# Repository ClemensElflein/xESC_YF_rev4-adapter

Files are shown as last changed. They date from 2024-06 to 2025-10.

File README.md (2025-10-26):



<!-- PROJECT SHIELDS -->
<!--
- Markdown "reference style" links for readability.
- Reference links are enclosed in brackets [ ] instead of parentheses ( ).
  (See the bottom of this document for the declaration of the reference variables)
-->
[][contributors-url]
[][forks-url]
[][stars-url]
[][issues-url]
[][license-url]

<!-- PROJECT LOGO -->
<br />
<div align="center">
<h3 align="center">xESC YardForce (Rev4) adapter for <a href="https://github.com/ClemensElflein/OpenMower">OpenMower</a></h3>

  <p align="center">
    Simple xESC adapter for stock Rev4 (built 2017) blade-motor<br>
    (the one with a internal motor controller under his cap)
    <br />
  </p>

  |             v1.x Hardware              |             v2.x Hardware              |
  | :------------------------------------: | :------------------------------------: |
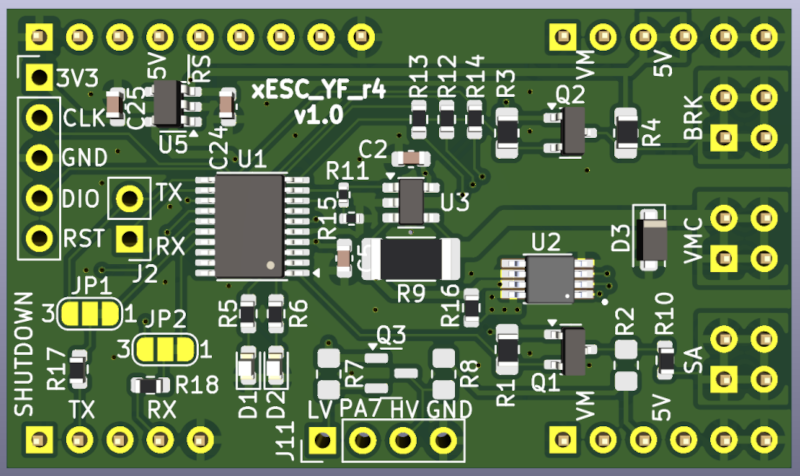
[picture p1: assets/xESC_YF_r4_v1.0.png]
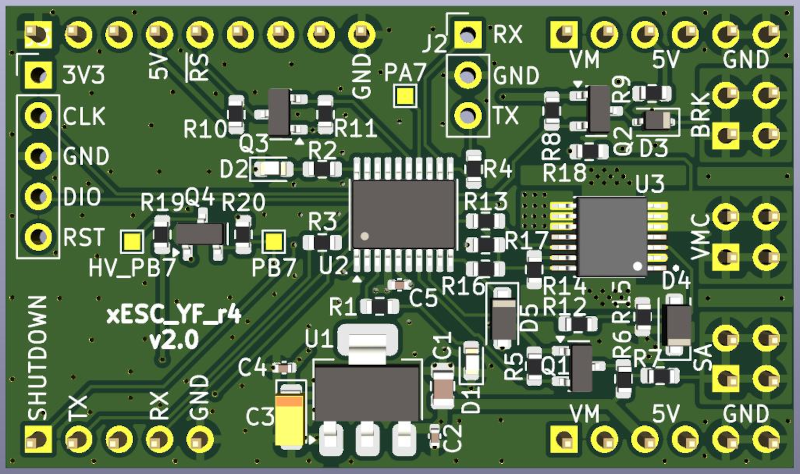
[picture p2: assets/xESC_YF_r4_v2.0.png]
  |  |  |

</div>

<!-- ABOUT THE PROJECT -->
## About The Project

<a href="assets/rev4-mow-motor.jpg">
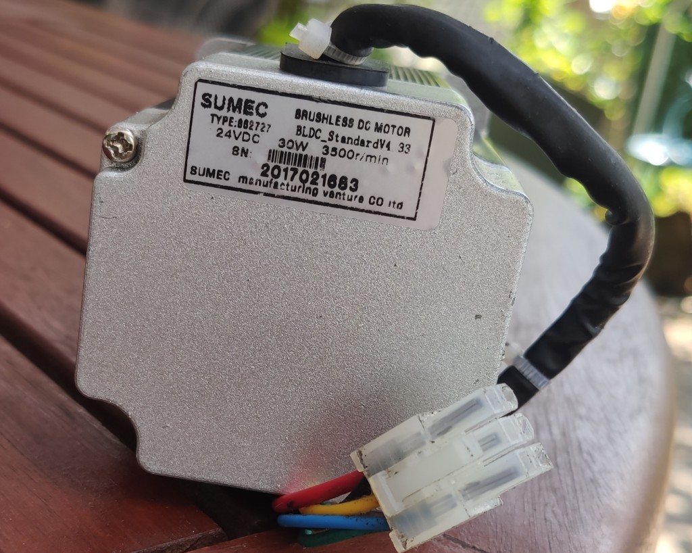
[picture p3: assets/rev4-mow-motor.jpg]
Rev.4 Mow Motor
  </a>

Those who want use <a href="https://github.com/ClemensElflein/OpenMower">OpenMower</a> with an older YardForce "Rev. 4" (built 2017) model, fail with the stock Blade-Motor as it has an embedded motor-controller under it's cap.

It's not very difficult to use this motor:
- Remove stock driver controller
- Wire the coil cables directly
- Add a 5 pin cable to the motor hall sensors
- Connect them to OM's mow-motor-hall-input plug
and use OM's xESC.

But it's somehow "crafted" and you need to be capable to do these things.

As an alternative, this "Adapter" is thought to replace OM's default Mow- xESC.<br>
In addition to this adapter, it's nevertheless **required to exchange two cables of the mow motor cabling**. But this should be also possible for the untalented (see [Requirements](#requirements)).

<p align="right">(<a href="#readme-top">back to top</a>)</p>

## Requirements

<a href="assets/cross-gn-bk.jpg">
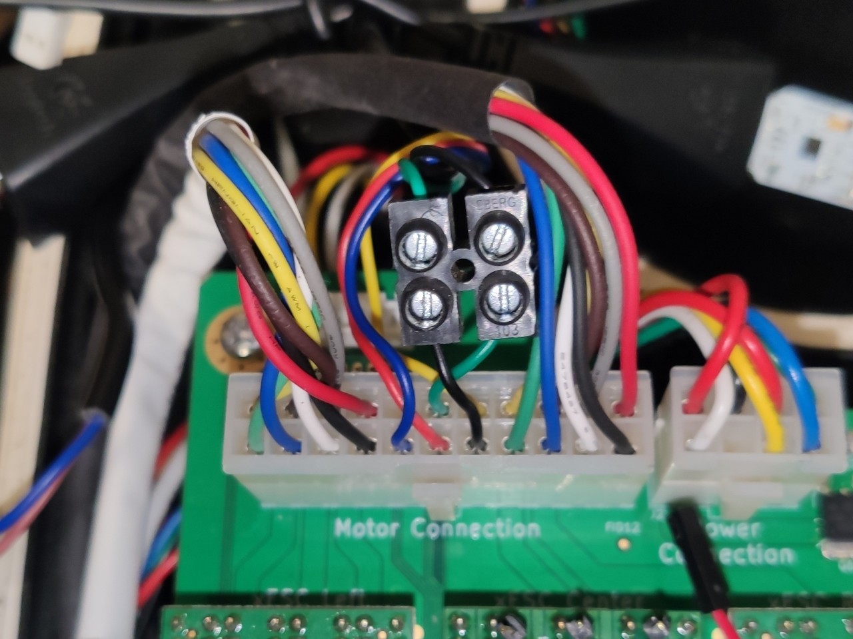
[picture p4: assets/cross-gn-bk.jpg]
Mandatory cable x-change
  </a>

**It's mandatory to cross the green and black mow-motor-cables!**

> [!WARNING]  
> **Never** plug or un-plug the mow-motor while the adapter is powered!

> [!WARNING]  
> Do **not** simply trust the cable colors!<br>
> Check the image and validate if your
> cables do have the same colors! If not adapt accordingly

Either exchange the pins within the plug, or do it the lazy way like me, with a luster terminal.
The latter has the advantage that you immediately see that you already crossed green/black.

## Prerequisites

* The compiled firmware, which can be found within the [Actions](https://github.com/ClemensElflein/xESC_YF_rev4-adapter/actions) section. Click the one you're intersted in (newest or tagged), scroll down to 'Artifacts', download and unzip to somewhere.
* As of writing, your openmower image has to be on edge version >= commit [0bfd489](https://github.com/ClemensElflein/open_mower_ros/commit/0bfd489401b3e659d183e6c1f9b557cb0d59d3c1) which happened on 2024-07-04

## Firmware Installation

### Requirements

* You need an ST-Link debugger/programmer, like one of the cheap "ST-Link V2" probes from one of the big online retailer.
* [STLINK Tools](https://github.com/stlink-org/stlink) >= v1.8.0 (earlier versions do **not** support the used STM32C0x MCU)

### Hardware Version Branding

Starting with hardware version 2.0, the adapters MCU needs to be branded by flashing a hardware config into the OTP area.

#### Branding Process:

1. **Generate** Hardware Config Binaries

   ```bash
   cd firmware/host-hw-config
   lbuild build
   scons
   ```

   This creates i.e.:
   - `hw_config_v1.0.bin` - Hardware v1.0 configuration
   - `hw_config_v2.0.bin` - Hardware v2.0 configuration
  
1. **Connect your ST-Link** to the adapter PCB. Do **not** connect the 3.3V pin if your adapter is already assembled to the OpenMower Mainboard and get powered by it!

1. **Flash** Hardware Config

   ```bash
   # Flash/Brand v2.0 config with ST-Link/V2
   STM32_Programmer_CLI -c port=SWD -d hw_config_v2.0.bin 0x1FFF7000
   ```

The branding process writes a small hardware information structure to the first two OTP dwords. **Take attention** that OTP flash can be written only once!

**Important Notes:**
- Branding only needs as well as "can" be done only **once per device**
- The branding **truly survives firmware updates** (because OTP flash can be written only once)
- Hardware Version 1.x boards don't need branding. Non-branded devices get assumed to be v1.0 hardware
<br>
<br>

**Firmware Installation Variants**

We've two options to install the firmware. Either via:<br>
- ST-Link debugger/programmer, for which you need to have access to the adapter PCB's SWDIO pins, or via
- Open-Mower's UART via STM32 internal bootloader (which can be done with a closed mower)

### Firmware Installation via ST-Link debugger/programmer

#### Flash

1. Connect your ST-Link probe to the adapter PCB. Do **not** connect the 3.3V pin if your adapter is already assembled to the OpenMower Mainboard and get powered by it!

2. Flash the adapter:
   ```sh
   st-flash --reset write firmware_xesc_yf_rev4.bin 0x08000000
   ```
   When done, st-flash should report 'Flash written and verified! jolly good!' (or similar) and immediately reboot.<br>

   **Only relevant for v1.x hardware:**

   > [!WARNING]  
   > Do not unplug now!
   
   On absolutely first firmware boot, it need to flash some settings to the MCU. You'll see some blink codes.<br>
   Do NOT unplug till you see:
   - 3 simultaneous blinks of the green+red LED (=success), following of a
   - quick blink of the red LED (=no motor connected) as well as a
   - normal green blink (=ROS not connected).
   
   The whole procedure will only take about 10 seconds. Once the procedure got processed it don't get triggered again for this MCU on future firmware flashes.

   If the board doesn't come up with blink signs, unplug and replug it. But once you see blink signs, do **not** unplug it before getting the described LED codes of the previous paragraph.   

<p align="right">(<a href="#readme-top">back to top</a>)</p>

### Firmware Installation via serial connection (UART)

Firmware flashing via UART is currently only possible with OpenMower V1 based hardware!

#### Requirements

* [STM32CubeProgrammer](https://www.st.com/en/development-tools/stm32cubeprog.html) is the tool we need to flash via UART. But because we like to use it with our OpenMower's Raspberry-Pi, we need it in `aarch64` architecture. Unfortunately (as well as unbelievable) ST's programmer tool for ARM CPU's isn't available *for* ARM CPU's/architectures!!<br>
So we need to trick a little bit, and for this you need a non-arm Linux machine (x86_64).<br>
  1. Download [STM32CubePrg-Lin](https://www.st.com/en/development-tools/stm32cubeprog.html) package with (or to) a x86_64 Linux machine
  2. Unpack and install it on the x86_64 Linux machine
  3. Pack (zip, tar, ...) the installed binaries from where you just installed them
  4. Copy that package to your Raspberry-Pi and unpack it to somewhere. I placed mine to /opt/STM32CubeProgrammer
* [box64](https://github.com/ptitSeb/box64) to be able to run the STM32CubeProgrammer's x86_64 binary with our aarch64 architecture.<br>
Luckily they do have pre-build [Debian packages](https://github.com/ptitSeb/box64/blob/main/docs/COMPILE.md#debian-based-linux). Please follow their instruction.

Once *box64* got installed, you should be able to start the STM32Programmer CLI i.e. via: `/opt/STM32CubeProgrammer/bin/STM32_Programmer_CLI`

### Flash

1. Login to your OpenMower Raspberry-Pi and stop openmower:<br>
   `sudo systemctl stop openmower`
   
2. Configure Raspberry-PI's serial device where the adapter is connected to, which is normally */dev/ttyAMA3*:<br>
   `stty -F /dev/ttyAMA3 115200 raw`
   
3. Now trigger the current running adapter firmware to do a reboot into the bootloader via:<br>
    `echo -e "\x00Reboot into Bootloader" > /dev/ttyAMA3`

4. Check if STM32 MCU is now in bootloader mode (Step 3. was successful):<br>
   `/opt/STM32CubeProgrammer/bin/STM32_Programmer_CLI -c port=/dev/ttyAMA3`<br>
   Should output something like:<br>

   ```
      -------------------------------------------------------------------
                        STM32CubeProgrammer v2.16.0                  
      -------------------------------------------------------------------

   Serial Port /dev/ttyAMA3 is successfully opened.
   Port configuration: parity = even, baudrate = 115200, data-bit = 8,
                       stop-bit = 1.0, flow-control = off
   Activating device: OK
   Board       : --
   Chip ID: 0x443 
   BootLoader protocol version: 3.1
   Device name : STM32C01x
   Flash size  : 32 KBytes (default)
   Device type : MCU
   Revision ID : --  
   Device CPU  : Cortex-M0+
   ```

5. Flash:<br>
   `/opt/STM32CubeProgrammer/bin/STM32_Programmer_CLI -c port=/dev/ttyAMA3 -w firmware_xesc_yf_rev4.bin 0x08000000`

6. Reset the device (start our newly flashed program):<br>
   `/opt/STM32CubeProgrammer/bin/STM32_Programmer_CLI -c port=/dev/ttyAMA3 --go 0x08000000`

   **Only relevant for v1.x hardware:**

   > [!WARNING]  
   > Do not power-off now!
   
   On absolutely first firmware boot, it need to flash some settings to the MCU. You'll see some blink codes.<br>
   Do NOT unplug till you see:
   - 3 simultaneous blinks of the green+red LED (=success), following of a
   - quick blink of the red LED (=no motor connected) as well as a
   - normal green blink (=ROS not connected).
   
   The whole procedure will only take about 10 seconds. Once the procedure got processed it don't get triggered again for this MCU on future firmware flashes.

7. Finally start openmower again:<br>
   `sudo systemctl start openmower`

<p align="right">(<a href="#readme-top">back to top</a>)</p>

## OpenMower Config

### OpenMower V1 based Hardware (mower_config)

Lastly, you need to add the adapter to your mower_config. Here's the relevant section out of mower_config.sh.example:

```
# Select your ESC type
# Supported values as of today:
# xesc_mini: for the STM32 version (VESC)
# xesc_mini_w_r4ma: for the STM32 version (VESC), but with Rev4 (Mow) Motor Adapter (only available for YardForceSA650 mower type)
# xesc_2040: for the RP2040 version (very experimental!)
# xesc_2040_w_r4ma: for the RP2040 version (very experimental!), but with Rev4 (Mow) Motor Adapter (only available for YardForceSA650 mower type)
export OM_MOWER_ESC_TYPE="xesc_mini"
```

Once adapted, restart openmower via: `sudo systemctl restart openmower`

### OpenMower V2 based Hardware: (xCore Firmware)

Edit OpenMower stack config via `openmower configure env` and set `FIRMWARE="yardforce-v4"`

<p align="right">(<a href="#readme-top">back to top</a>)</p>

## LED codes

<table>
  <tr><th>Green</th><th>Red</th><th>Description</th></tr>
  <tr><td colspan="2" align="center">3 * quick blink</td><td>'Power up' successful</td></tr>
  <tr><td>1Hz blink</td><td></td><td>Waiting for init by xesc_ros</td></tr>
  <tr><td>0.5Hz flash<br>(short flash every 2 seconds)</td><td></td><td>Shutdown (Sleep) triggered by OpenMower Pico FW</td></tr>
  <tr><td>on</td><td></td><td>All fine (initialized, xesc_ros connected and no error)</td></tr>  
  <tr><td></td><td>1Hz blink</td><td>Waiting for OpenMower (xesc_ros driver) connect</td></tr>
  <tr><td></td><td>flash</td><td>One single short flash for every host communication error, like packet or CRC error</td></tr>
  <tr><td></td><td>on</td><td><b>Wrong hardware version firmware flashed!</b><br>Motor disabled for safety. Flash correct firmware</td></tr>
  <tr><td></td><td>5 * blink</td><td>NRST Pin not yet disabled. <b>Keep board powered</b> and watch for further LED codes</td></tr>
  <tr><td>5 * blink</td><td></td><td>NRST successful flashed</td></tr>
  <tr><td></td><td>4Hz quick blink</td><td>Open VMC (no motor connected).<br> <b>WARNING:</b> Do not connect the motor while the adapter is powered!</td></tr>
  <tr><td></td><td>2Hz fast blink</td><td>VMS temperature issue or over-current detected</td></tr>
</table>

<p align="right">(<a href="#readme-top">back to top</a>)</p>

## Self-Compile

This project is build with [modm](https://modm.io). You need to install the required toolchain as described in their [Installation](https://modm.io/guide/installation/) section, before going on.

Once done:

1. Clone this repository (inclusive submodules):<br>
  `git clone --recurse-submodules https://github.com/ClemensElflein/xESC_YF_rev4-adapter.git`
2. Change into the project source directory:<br>
  `cd xESC_YF_rev4-adapter/firmware/src`
3. Build the modm library files for a specific hardware version:<br>
   ```bash
   # This is for v2.0 hardware building
   lbuild -c hw-v2.xml build
   ```
4. Compile the firmware binary:<br>
  `scons [profile=<release|debug>] [build]`
5. Flash firmware:<br>
  For this, a specific [xPack OpenOCD](https://xpack-dev-tools.github.io/openocd-xpack/) version is required. Either install your own one, or use the one within the package folder by:<br>
  `export MODM_OPENOCD_BINARY=../packages/xpack-openocd-0.12.0-3-linux-x64/bin/openocd`<br>
  Afterwards flash the firmware via:<br>
  `scons program`

<p align="right">(<a href="#readme-top">back to top</a>)</p>

## Roadmap

(Ordered by priority)

- [x] Design schematics and PCB 
- [x] Produce PCB
- [ ] Firmware 
    - [x] Generic VM control (on/off)
    - [x] Generic motor control (start, stop, break)
    - [x] Read SA, math RPM
    - [x] Open VMC (no motor connected) detection
    - [x] Disable NRST pin functionality
    - [x] Motor current consumption
    - [x] PCB temperature (junction temp of STM)
    - [x] Support shutdown signal
    - [ ] ~~Stock motor (wrong) cabling detection~~
    - [x] STM32 bootloader / flash via UART support (OpenMower V1 based mainboard)
    - [ ] UART flash support for OpenMower V2 based carrier-boards
- [x] ROS driver
    - [x] xesc_ros::xesc_yfr4
    - [x] Add RPM
- [x] OpenMower Hardware V2 firmware driver

See the [open issues](https://github.com/ClemensElflein/xESC_YF_rev4-adapter/issues) for a full list of proposed features (and known issues).

<p align="right">(<a href="#readme-top">back to top</a>)</p>

## History

  | Version | Release Date | Info                                                                                                                                                                                          |
  | ------- | :----------: | --------------------------------------------------------------------------------------------------------------------------------------------------------------------------------------------- |
  | 0.3.0   |  2025-10-25  | - Fix "Open-Load" detection for Rev4-ESC hardware v1.0<br>- Improve load current and RPM calculations<br>- Add hardware/firmware mixup protection<br>- Add support for Rev4-ESC hardware v2.x |
  | 0.2.3   |  2024-10-03  | - Add RPM to status package                                                                                                                                                                   |
  | 0.2.2   |  2024-08-25  | - Support STM32 bootloader flash via UART                                                                                                                                                     |
  | 0.2.1   |  2024-08-19  | - Add shutdown signal handling (sleep/power-off VMC)<br>- Handle over-temp and over-current                                                                                                   |
  | 0.2.0   |  2024-08-16  | - Switch from Arduino to modm lib<br>- Integrate flash procedure to disable-NRST<br>- Add Motor current and PCB temperature                                                                   |
  | 0.1.1   |  2024-07-10  | - Open VMC (no motor connected) detection<br>- VMC-short and thermal error detection                                                                                                          |
  | 0.1.0   |  2024-07-05  | Generic functionality like Start, Stop, Break                                                                                                                                                 |

<p align="right">(<a href="#readme-top">back to top</a>)</p>

<!-- CONTRIBUTING -->
## Contributing

Contributions are what make the open source community such an amazing place to learn, inspire, and create. Any contributions you make are **greatly appreciated**.

If you have a suggestion that would make this better, please fork the repo and create a pull request. You can also simply open an issue with the tag "enhancement".
Don't forget to give the project a star! Thanks again!

1. Fork the Project
2. Create your Feature Branch (`git checkout -b feature/AmazingFeature`)
3. Commit your Changes (`git commit -m 'Add some AmazingFeature'`)
4. Push to the Branch (`git push origin feature/AmazingFeature`)
5. Open a Pull Request

<p align="right">(<a href="#readme-top">back to top</a>)</p>

<!-- LICENSE -->
## License

Distributed under the MIT License. See `LICENSE.txt` for more information.

<p align="right">(<a href="#readme-top">back to top</a>)</p>

<!-- CONTACT -->
## Contact

Project Link: [https://github.com/ClemensElflein/xESC_YF_rev4-adapter](https://github.com/ClemensElflein/xESC_YF_rev4-adapter)

<p align="right">(<a href="#readme-top">back to top</a>)</p>

<!-- MARKDOWN LINKS & IMAGES -->
<!-- https://www.markdownguide.org/basic-syntax/#reference-style-links -->
[contributors-shield]: https://img.shields.io/github/contributors/ClemensElflein/xESC_YF_rev4-adapter.svg?style=for-the-badge
[contributors-url]: https://github.com/ClemensElflein/xESC_YF_rev4-adapter/graphs/contributors
[forks-shield]: https://img.shields.io/github/forks/ClemensElflein/xESC_YF_rev4-adapter.svg?style=for-the-badge
[forks-url]: https://github.com/ClemensElflein/xESC_YF_rev4-adapter/network/members
[stars-shield]: https://img.shields.io/github/stars/ClemensElflein/xESC_YF_rev4-adapter.svg?style=for-the-badge
[stars-url]: https://github.com/ClemensElflein/xESC_YF_rev4-adapter/stargazers
[issues-shield]: https://img.shields.io/github/issues/ClemensElflein/xESC_YF_rev4-adapter.svg?style=for-the-badge
[issues-url]: https://github.com/ClemensElflein/xESC_YF_rev4-adapter/issues
[license-shield]: https://img.shields.io/github/license/ClemensElflein/xESC_YF_rev4-adapter.svg?style=for-the-badge
[license-url]: https://github.com/ClemensElflein/xESC_YF_rev4-adapter/blob/master/LICENSE.txt

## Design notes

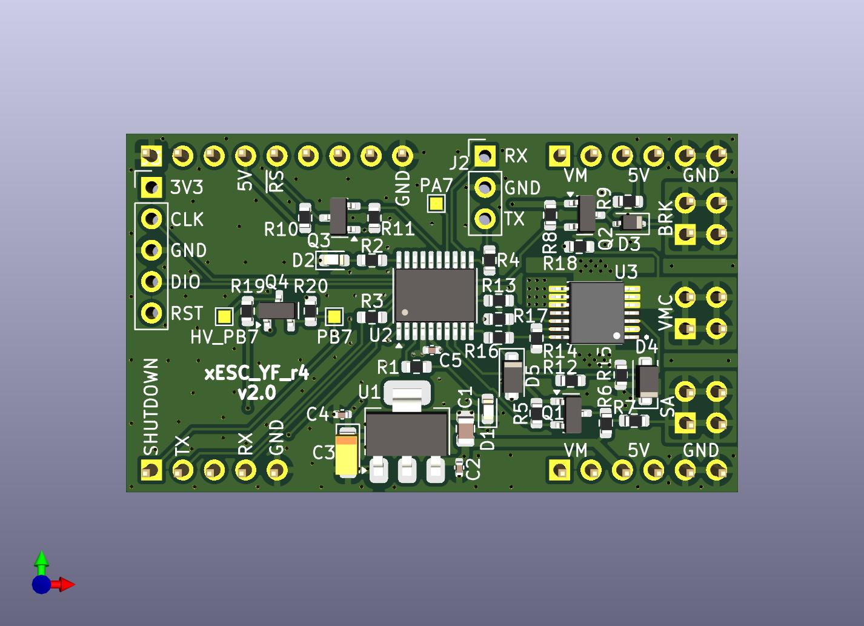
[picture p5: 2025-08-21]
PCB/xESC_YF_r4.jpg

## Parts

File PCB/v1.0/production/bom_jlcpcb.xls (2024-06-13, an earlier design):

Comment | Designator | Footprint | JLCPCB Part #
INA139NA | U3 | SOT-23-5 | C129947
75mR | R9 | 2010 | C333474
S2MW | D3 | D_SOD-123F | C128729
TPS1H200A | U2 | SOP65P490X110-9N | C2653785
15k | R16 | 0603 | C22809
150R | R5,R6 | 0603 | C22808
100 | R10 | 0603 | C22775
LEDGREEN | D1 | 0603 | C12624
STM32C011F6P6 | U1 | TSSOP-20_4.4x6.5mm_P0.65mm | C5456198
LEDRED | D2 | 0603 | C2286
1k | R1,R2,R3,R4,R7,R8 | 0805 | C95781
.1uF | C2,C5 | 0603 | C15849
220 | R17,R18 | 0603 | C22962
4k7 | R12,R13,R14 | 0603 | C23162
4.7uF/16V | C24,C25 | 0603 | C19666
20k | R11,R15 | 0402 | C25765
BSS138 | Q1,Q2,Q3 | SOT-23 | C3040446
XC6220B331MR | U5 | SOT-23-5 | C86534

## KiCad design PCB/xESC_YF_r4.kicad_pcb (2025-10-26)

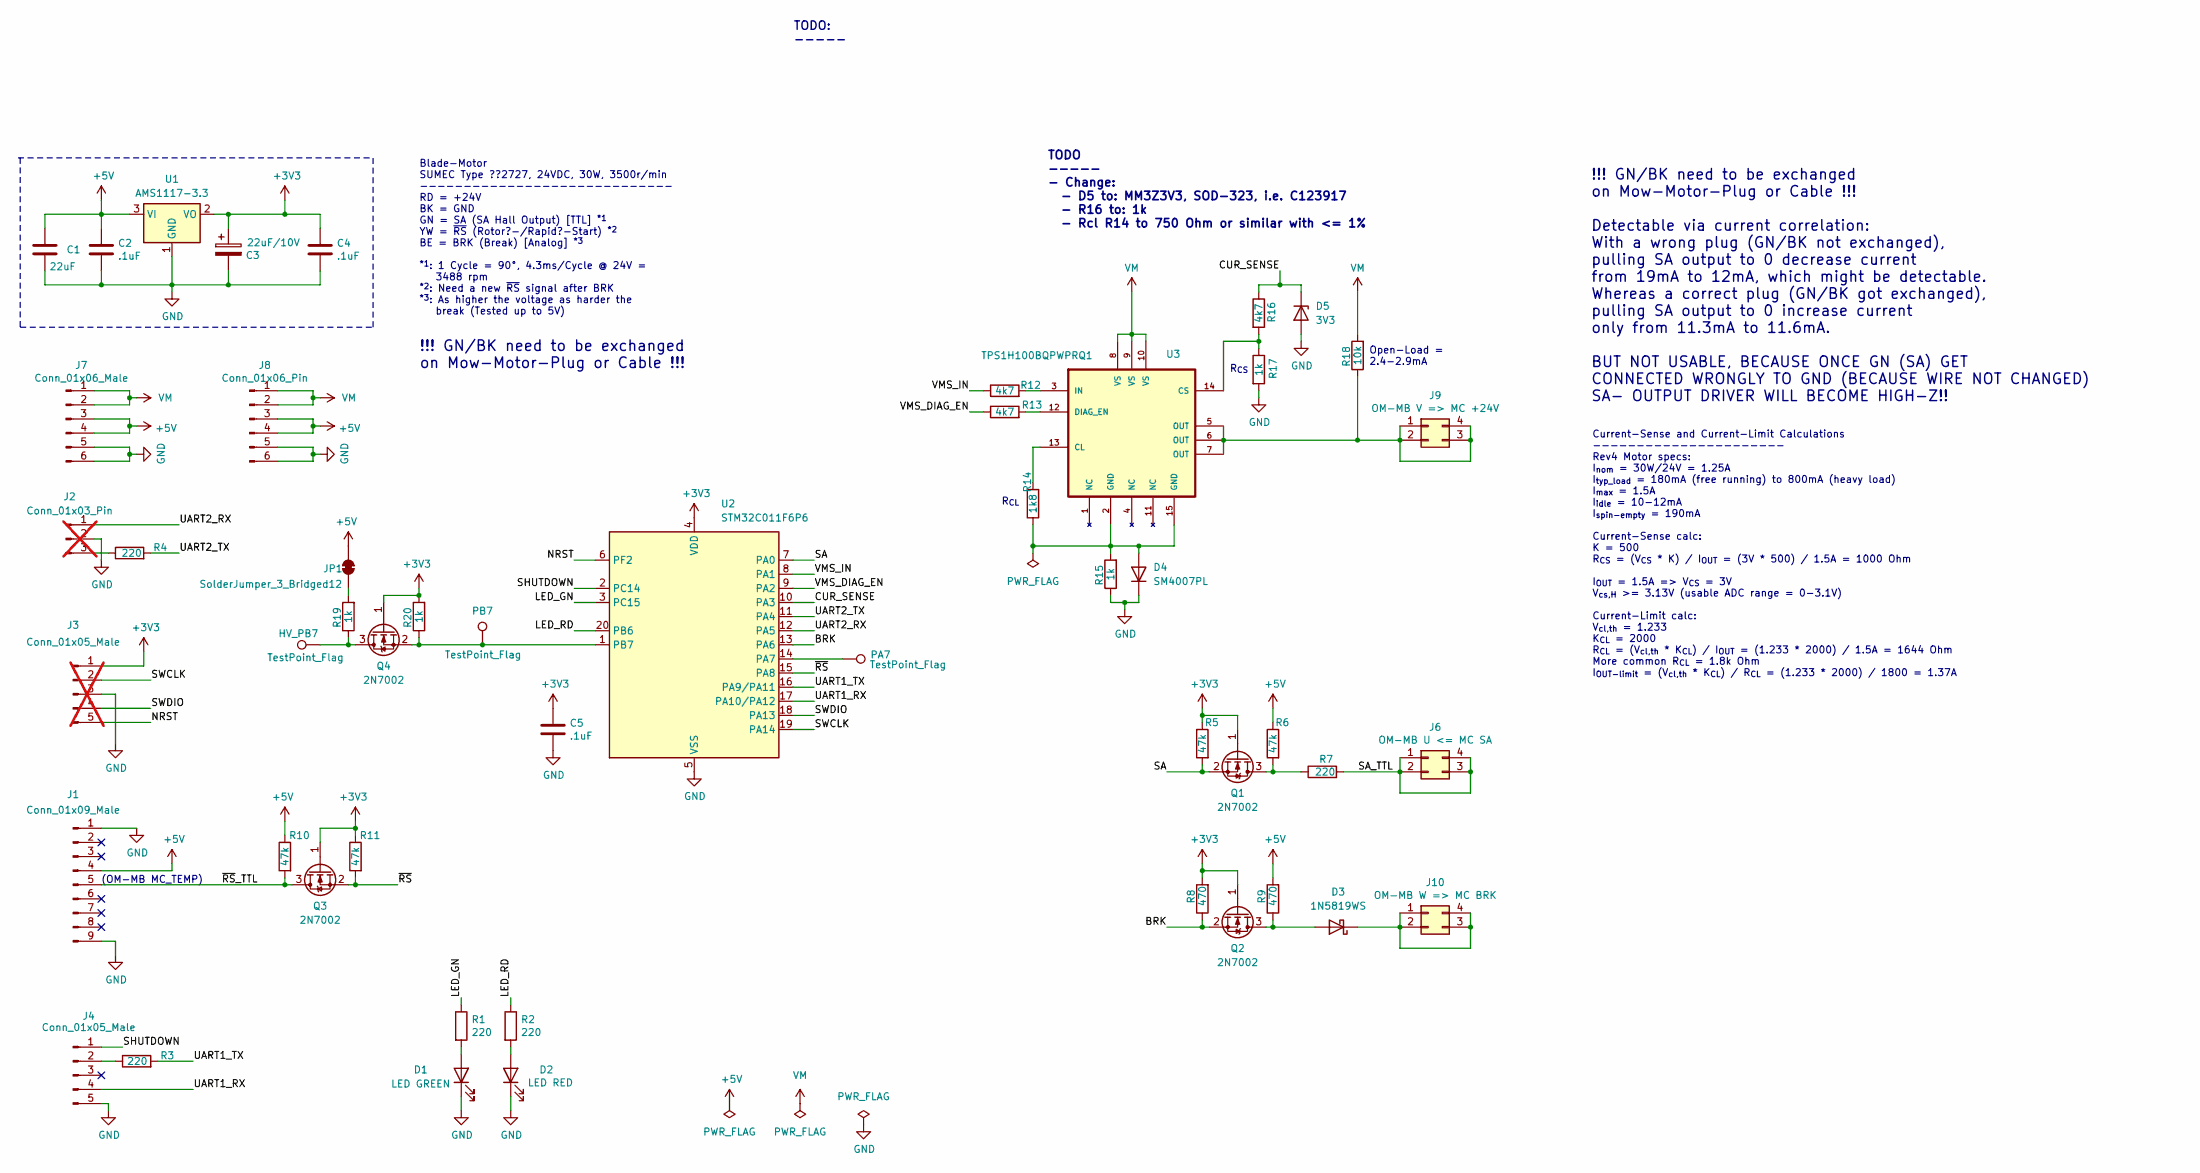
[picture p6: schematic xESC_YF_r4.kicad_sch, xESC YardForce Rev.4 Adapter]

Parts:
C1: 22uF; C_0805_2012Metric; LCSC C45783
C2, C4, C5: .1uF; C_0402_1005Metric; LCSC C1525
C3: 22uF/10V; CP_EIA-3216-10_Kemet-I; LCSC C129272
D1: LED GREEN; LED_0603_1608Metric; Part Number LTST-C191KGKT; Digikey 160-1446-1-ND
D2: LED RED; LED_0603_1608Metric; Part Number LTST-C191KRKT; Digikey 160-1447-1-ND
D3: 1N5819WS; D_SOD-323; LCSC C191023
D4: SM4007PL; D_SOD-123F; LCSC C64898
D5: 3V3; D_SOD-123F; MFR PART MMSZ4684T1G; LCSC C24672
HV_PB7: TestPoint_Flag; TestPoint_Pad_1.0x1.0mm
J1: Conn_01x09_Male; PinHeader_1x09_P2.54mm_Vertical; Part Number DZ254R-11-09-63; LCSC C2935915
J2: Conn_01x03_Pin; PinHeader_1x03_P2.54mm_Vertical; not fitted
J3: Conn_01x05_Male; PinHeader_1x05_P2.54mm_Vertical; Part Number DZ254R-11-05-63; LCSC C2935911; not fitted
J4: Conn_01x05_Male; PinHeader_1x05_P2.54mm_Vertical; Part Number DZ254R-11-05-63; LCSC C2935911
J6: OM-MB U <= MC SA; PinHeader_2x02_P2.54mm_Vertical; Part Number B-2100S04P-B110; LCSC C124362
J7: Conn_01x06_Male; PinHeader_1x06_P2.54mm_Vertical; Part Number DZ254R-11-06-63; LCSC C2935912
J8: Conn_01x06_Pin; PinHeader_1x06_P2.54mm_Vertical; Part Number DZ254R-11-06-63; LCSC C2935912
J9: OM-MB V => MC +24V; PinHeader_2x02_P2.54mm_Vertical; Part Number B-2100S04P-B110; LCSC C124362
J10: OM-MB W => MC BRK; PinHeader_2x02_P2.54mm_Vertical; Part Number B-2100S04P-B110; LCSC C124362
JP1: SolderJumper_3_Bridged12; SolderJumper-2_P1.3mm_Bridged_RoundedPad1.0x1.5mm
PA7: TestPoint_Flag; TestPoint_Pad_1.0x1.0mm
PB7: TestPoint_Flag; TestPoint_Pad_1.0x1.0mm
Q1, Q2, Q3, Q4: 2N7002; SOT-23; LCSC C8545
R1, R2, R7: 220; R_0603_1608Metric; LCSC C22962
R3, R4: 220; R_0603_1608Metric; Part Number 0603WAF2200T5E; LCSC C22962
R5, R6, R10, R11: 47k; R_0603_1608Metric; Part Number 0603WAF4702T5E; LCSC C25819
R8, R9: 470; R_0603_1608Metric; Part Number 0603WAF4700T5E; LCSC C23179
R12, R13, R16: 4k7; R_0603_1608Metric; Part Number 0603WAF4701T5E; LCSC C23162
R14: 1k8; R_0603_1608Metric; Part Number 0603WAF1801T5E; LCSC C4177
R15, R17, R19, R20: 1k; R_0603_1608Metric; Part Number 0603WAF1001T5E; LCSC C21190
R18: 10k; R_0603_1608Metric; Part Number 0603WAF1002T5E; LCSC C25804
U1: AMS1117-3.3; SOT-223-3_TabPin2; LCSC C6186
U2: STM32C011F6P6; TSSOP-20_4.4x6.5mm_P0.65mm; JLCPCB C5456198
U3: TPS1H100BQPWPRQ1; TPS1H100-Q1_ThermalVias; LCSC C475505

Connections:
+3V3: C3.1, C4.1, C5.1, J3.1, Q1.1 (G), Q2.1 (G), Q3.1 (G), Q4.1 (G), R5.1, R8.2, R11.1, R20.2, U1.2 (VO), U2.4 (VDD)
+5V: C1.1, C2.1, J1.4, J7.3, J7.4, J8.3, J8.4, JP1.2 (B), R6.1, R9.2, R10.1, U1.3 (VI)
/BRK: Q2.2 (S), R8.1, U2.13 (PA6)
/CUR_SENSE: D5.1 (K), R16.1, U2.10 (PA3)
/LED_GN: R1.1, U2.3 (PC15)
/LED_RD: R2.1, U2.20 (PB6)
/NRST: J3.5, U2.6 (PF2)
/SA: Q1.2 (S), R5.2, U2.7 (PA0)
/SA_TTL: J6.1, J6.2, J6.3, J6.4, R7.2
/SHUTDOWN: J4.1, U2.2 (PC14)
/SWCLK: J3.2, U2.19 (PA14)
/SWDIO: J3.4, U2.18 (PA13)
/UART1_RX: J4.4, U2.17 (PA10/PA12)
/UART1_TX: R3.2, U2.16 (PA9/PA11)
/UART2_RX: J2.1, U2.12 (PA5)
/UART2_TX: R4.2, U2.11 (PA4)
/VMS_DIAG_EN: R13.1, U2.9 (PA2)
/VMS_IN: R12.1, U2.8 (PA1)
/~RS: Q3.2 (S), R11.2, U2.15 (PA8)
/~RS_TTL: J1.5, Q3.3 (D), R10.2
GND: C1.2, C2.2, C3.2, C4.2, C5.2, D1.1 (K), D2.1 (K), D4.1 (K), D5.2 (A), J1.1, J1.9, J2.2, J3.3, J4.5, J7.5, J7.6, J8.5, J8.6, R15.1, R17.2, U1.1 (GND), U2.5 (VSS)
unnamed: D1.2 (A), R1.2
unnamed: D2.2 (A), R2.2
unnamed: D3.2 (A), Q2.3 (D), R9.1
unnamed: D3.1 (K), J10.1, J10.2, J10.3, J10.4
unnamed: D4.2 (A), R14.1, R15.2, U3.2 (GND), U3.15 (GND)
unnamed: J2.3, R4.1
unnamed: J4.2, R3.1
unnamed: J9.1, J9.2, J9.3, J9.4, R18.1, U3.5 (OUT), U3.6 (OUT), U3.7 (OUT)
unnamed: JP1.1 (A), R19.2
unnamed: Q1.3 (D), R6.2, R7.1
unnamed: HV_PB7.1, Q4.3 (D), R19.1
unnamed: PB7.1, Q4.2 (S), R20.1, U2.1 (PB7)
unnamed: PA7.1, U2.14 (PA7)
unnamed: R14.2, U3.13 (CL)
unnamed: R16.2, R17.1, U3.14 (CS)
unnamed: R13.2, U3.12 (DIAG_EN)
unnamed: R12.2, U3.3 (IN)
VM: J7.1, J7.2, J8.1, J8.2, R18.2, U3.8 (VS), U3.9 (VS), U3.10 (VS)

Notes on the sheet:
(OM-MB MC_TEMP)
Current-Sense and Current-Limit Calculations ---------------------- Rev4 Motor specs: I_{nom} = 30W/24V = 1.25A I_{typ_load} = 180mA (free running) to 800mA (heavy load) I_{max} = 1.5A I_{idle} = 10-12mA I_{spin-empty} = 190mA Current-Sense calc: K = 500 R_{CS} = (V_{CS} * K) / I_{OUT} = (3V * 500)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
TODO: -----
!!! GN/BK need to be exchanged on Mow-Motor-Plug or Cable !!! Detectable via current correlation: With a wrong plug (GN/BK not exchanged), pulling SA output to 0 decrease current from 19mA to 12mA, which might be detectable. Whereas a correct plug (GN/BK got exchanged), pulling SA output to 0 incre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
Open-Load = 2.4-2.9mA
Blade-Motor SUMEC Type ??2727, 24VDC, 30W, 3500r/min ----------------------------- RD = +24V BK = GND GN = SA (SA Hall Output) [TTL] ^{*1} YW = ~{RS} (Rotor?-/Rapid?-Start) ^{*2} BE = BRK (Break) [Analog] ^{*3} ^{*1}: 1 Cycle = 90°, 4.3ms/Cycle @ 24V = 3488 rpm ^{*2}: Need a new ~{RS} signal after 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
!!! GN/BK need to be exchanged on Mow-Motor-Plug or Cable !!!
TODO ----- - Change: - D5 to: MM3Z3V3, SOD-323, i.e. C123917 - R16 to: 1k - Rcl R14 to 750 Ohm or similar with <= 1%
R_{CL}
R_{CS}

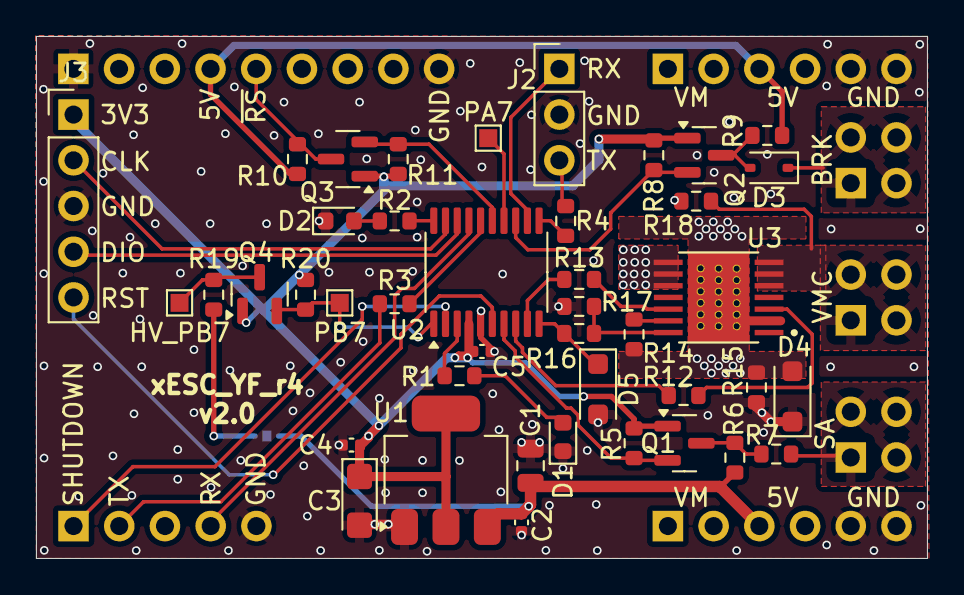
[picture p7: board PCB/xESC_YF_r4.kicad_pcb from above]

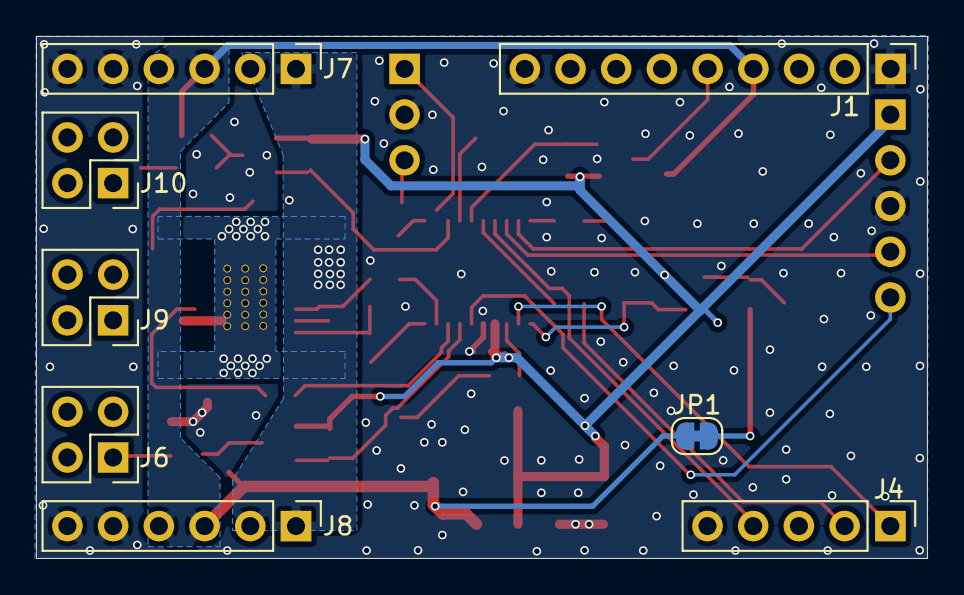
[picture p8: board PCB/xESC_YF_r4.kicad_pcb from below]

Board: 2 copper layers, 49.5 x 29.0 mm, 50 parts (8 on the bottom side), 39 nets.

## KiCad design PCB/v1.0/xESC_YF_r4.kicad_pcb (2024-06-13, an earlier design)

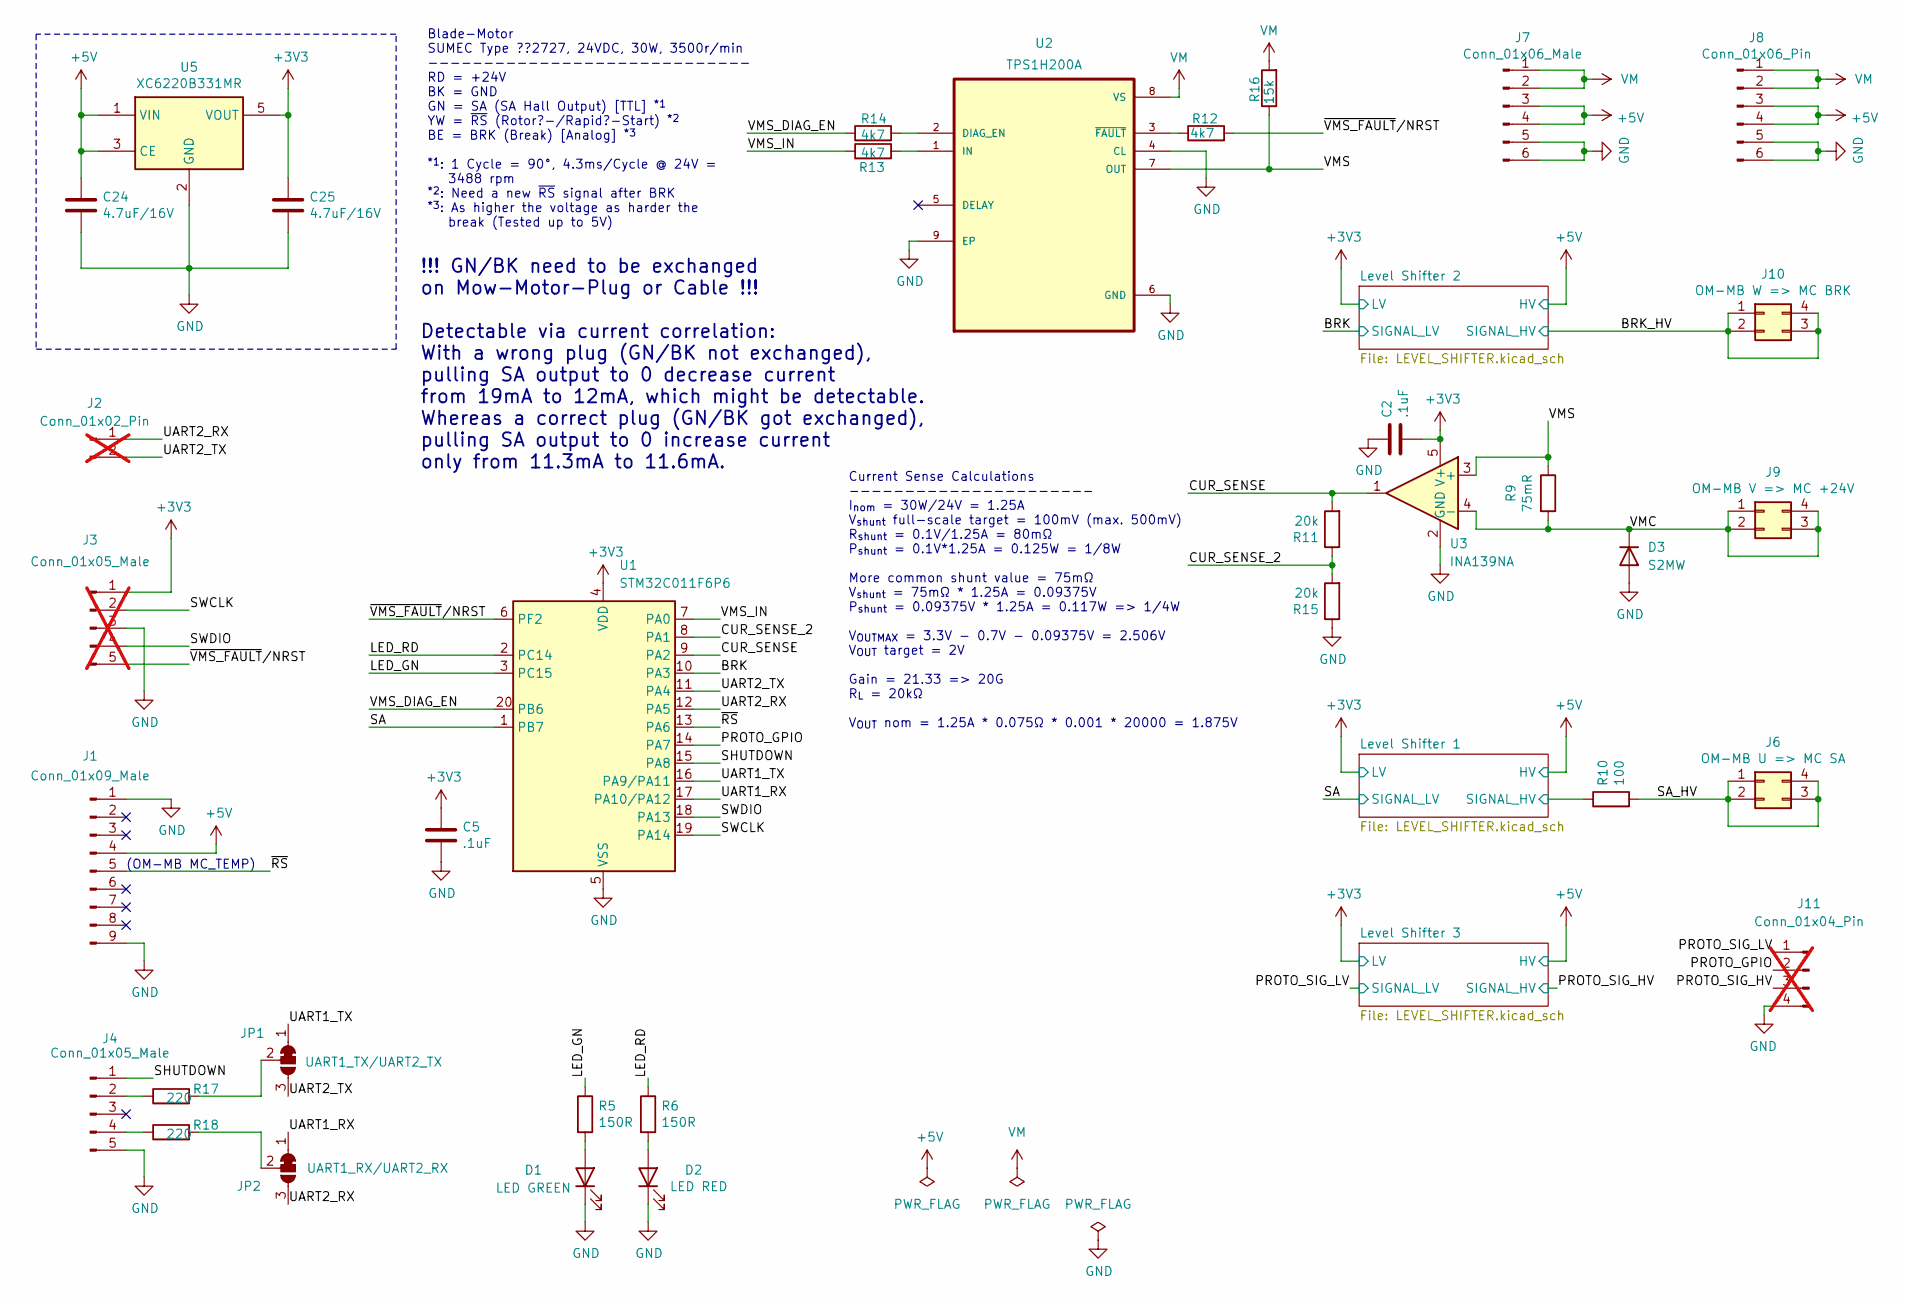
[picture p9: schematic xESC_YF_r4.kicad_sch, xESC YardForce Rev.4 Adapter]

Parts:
C2, C5: .1uF; C_0603_1608Metric; Part Number CL10B104KC8NNNC; Digikey 1276-1935-1-ND
C24, C25: 4.7uF/16V; C_0603_1608Metric; Part Number CL21A106KOQNNNE; Digikey 1276-1096-2-ND
D1: LED GREEN; LED_0603_1608Metric; Part Number LTST-C191KGKT; Digikey 160-1446-1-ND
D2: LED RED; LED_0603_1608Metric; Part Number LTST-C191KRKT; Digikey 160-1447-1-ND
D3: S2MW; D_SOD-123F; Part Number S2MW; JLCPCB C2900725
J1: Conn_01x09_Male; PinHeader_1x09_P2.54mm_Vertical; Part Number DZ254R-11-09-63; LCSC C2935915
J2: Conn_01x02_Pin; PinHeader_1x02_P2.54mm_Vertical; not fitted
J3: Conn_01x05_Male; PinHeader_1x05_P2.54mm_Vertical; Part Number DZ254R-11-05-63; LCSC C2935911; not fitted
J4: Conn_01x05_Male; PinHeader_1x05_P2.54mm_Vertical; Part Number DZ254R-11-05-63; LCSC C2935911
J6: OM-MB U => MC SA; PinHeader_2x02_P2.54mm_Vertical; Part Number B-2100S04P-B110; LCSC C124362
J7: Conn_01x06_Male; PinHeader_1x06_P2.54mm_Vertical; Part Number DZ254R-11-06-63; LCSC C2935912
J8: Conn_01x06_Pin; PinHeader_1x06_P2.54mm_Vertical; Part Number DZ254R-11-06-63; LCSC C2935912
J9: OM-MB V => MC +24V; PinHeader_2x02_P2.54mm_Vertical; Part Number B-2100S04P-B110; LCSC C124362
J10: OM-MB W => MC BRK; PinHeader_2x02_P2.54mm_Vertical; Part Number B-2100S04P-B110; LCSC C124362
J11: Conn_01x04_Pin; PinHeader_1x04_P2.54mm_Vertical; not fitted
JP1: UART1_TX/UART2_TX; SolderJumper-3_P1.3mm_Bridged12_RoundedPad1.0x1.5mm_NumberL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
JP2: UART1_RX/UART2_RX; SolderJumper-3_P1.3mm_Bridged12_RoundedPad1.0x1.5mm_NumberL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
R5, R6: 150R; R_0603_1608Metric; Part Number RC0603FR-07150RL; Digikey 311-150HRCT-ND
R9: 75mR; R_2010_5025Metric_Pad1.40x2.65mm_HandSolder; Part Number RTT20R075FTE; JLCPCB C333474
R10: 100; R_0603_1608Metric
R11, R15: 20k; R_0402_1005Metric; Part Number RK73G1ETTP2002D; JLCPCB C2579762
R12, R13, R14: 4k7; R_0603_1608Metric; Part Number RC0603FR-07150RL; Digikey 311-150HRCT-ND
R16: 15k; R_0603_1608Metric
R17, R18: 220; R_0603_1608Metric
U1: STM32C011F6P6; TSSOP-20_4.4x6.5mm_P0.65mm; JLCPCB C5456198
U2: TPS1H200A; SOP65P490X110-9N; JLCPCB C2653785
U3: INA139NA; SOT-23-5
U5: XC6220B331MR; SOT-23-5; Part Number XC6220B331MR; Digikey 893-1133-1-ND

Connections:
+3V3: C2.2, C5.1, C25.1, J3.1, U1.4 (VDD), U3.5 (V+), U5.5 (VOUT); also elsewhere on the board
+5V: C24.1, J1.4, J7.3, J7.4, J8.3, J8.4, U5.1 (VIN), U5.3 (CE); also elsewhere on the board
/BRK: U1.10 (PA3); also elsewhere on the board
/BRK_HV: J10.1, J10.2, J10.3, J10.4; also elsewhere on the board
/CUR_SENSE: R11.2, U1.9 (PA2), U3.1
/CUR_SENSE_2: R11.1, R15.2, U1.8 (PA1)
/LED_GN: R5.1, U1.3 (PC15)
/LED_RD: R6.1, U1.2 (PC14)
/Level Shifter 1/SIGNAL_HV: R10.1; also elsewhere on the board
/PROTO_GPIO: J11.2, U1.14 (PA7)
/PROTO_SIG_HV: J11.3; also elsewhere on the board
/PROTO_SIG_LV: J11.1; also elsewhere on the board
/SA: U1.1 (PB7); also elsewhere on the board
/SA_HV: J6.1, J6.2, J6.3, J6.4, R10.2
/SHUTDOWN: J4.1, U1.15 (PA8)
/SWCLK: J3.2, U1.19 (PA14)
/SWDIO: J3.4, U1.18 (PA13)
/UART1_RX: JP2.1 (A), U1.17 (PA10/PA12)
/UART1_TX: JP1.1 (A), U1.16 (PA9/PA11)
/UART2_RX: J2.1, JP2.3 (B), U1.12 (PA5)
/UART2_TX: J2.2, JP1.3 (B), U1.11 (PA4)
/VMC: D3.1 (K), J9.1, J9.2, J9.3, J9.4, R9.2, U3.4 (-)
/VMS: R9.1, R16.1, U2.7 (OUT), U3.3 (+)
/VMS_DIAG_EN: R14.1, U1.20 (PB6)
/VMS_IN: R13.1, U1.7 (PA0)
/~RS: J1.5, U1.13 (PA6)
/~VMS_FAULT/NRST: J3.5, R12.2, U1.6 (PF2)
GND: C2.1, C5.2, C24.2, C25.2, D1.1 (K), D2.1 (K), D3.2 (A), J1.1, J1.9, J3.3, J4.5, J7.5, J7.6, J8.5, J8.6, J11.4, R15.1, U1.5 (VSS), U2.4 (CL), U2.6 (GND), U2.9 (EP), U3.2 (GND), U5.2 (GND)
unnamed: D1.2 (A), R5.2
unnamed: D2.2 (A), R6.2
unnamed: J4.2, R17.1
unnamed: J4.4, R18.1
unnamed: JP1.2 (C), R17.2
unnamed: JP2.2 (C), R18.2
unnamed: R14.2, U2.2 (DIAG_EN)
unnamed: R13.2, U2.1 (IN)
unnamed: R12.1, U2.3 (~FAULT)
VM: J7.1, J7.2, J8.1, J8.2, R16.2, U2.8 (VS)

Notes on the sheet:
(OM-MB MC_TEMP)
Blade-Motor SUMEC Type ??2727, 24VDC, 30W, 3500r/min ----------------------------- RD = +24V BK = GND GN = SA (SA Hall Output) [TTL] ^{*1} YW = ~{RS} (Rotor?-/Rapid?-Start) ^{*2} BE = BRK (Break) [Analog] ^{*3} ^{*1}: 1 Cycle = 90°, 4.3ms/Cycle @ 24V = 3488 rpm ^{*2}: Need a new ~{RS} signal after 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
!!! GN/BK need to be exchanged on Mow-Motor-Plug or Cable !!! Detectable via current correlation: With a wrong plug (GN/BK not exchanged), pulling SA output to 0 decrease current from 19mA to 12mA, which might be detectable. Whereas a correct plug (GN/BK got exchanged), pulling SA output to 0 incre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
Current Sense Calculations ---------------------- I_{nom} = 30W/24V = 1.25A V_{shunt} full-scale target = 100mV (max. 500mV) R_{shunt} = 0.1V/1.25A = 80mΩ P_{shunt} = 0.1V*1.25A = 0.125W = 1/8W More common shunt value = 75mΩ V_{shunt} = 75mΩ * 1.25A = 0.09375V P_{shunt} = 0.09375V * 1.25A = 0.117W 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

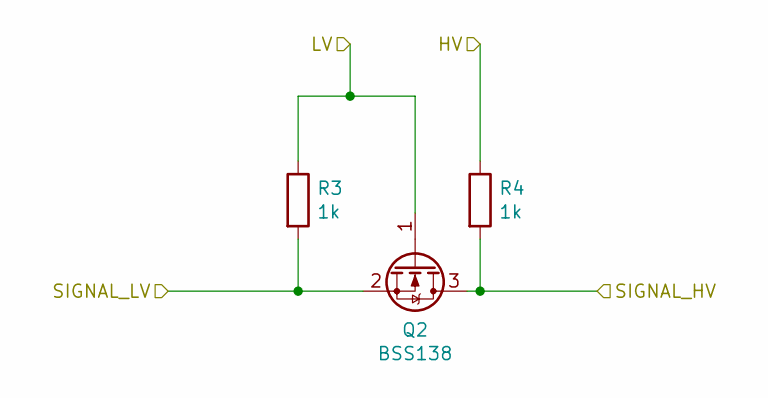
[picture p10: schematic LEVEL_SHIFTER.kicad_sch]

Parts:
Q2: BSS138; SOT-23; Part Number AP2300; LCSC C3040446
R3, R4: 1k; R_0805_2012Metric_Pad1.20x1.40mm_HandSolder; Part Number RC0805FR-071KL; Digikey 311-1.00KCRCT-ND

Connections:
+3V3: Q2.1 (G), R3.1; also elsewhere on the board
+5V: R4.1; also elsewhere on the board
/BRK: Q2.2 (S), R3.2; also elsewhere on the board
/BRK_HV: Q2.3 (D), R4.2; also elsewhere on the board

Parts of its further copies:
Q1, Q3: BSS138; SOT-23; Part Number AP2300; LCSC C3040446
R1, R2, R7, R8: 1k; R_0805_2012Metric_Pad1.20x1.40mm_HandSolder; Part Number RC0805FR-071KL; Digikey 311-1.00KCRCT-ND

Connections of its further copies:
+3V3: Q1.1 (G), Q3.1 (G), R1.1, R7.1; also elsewhere on the board
+5V: R2.1, R8.1; also elsewhere on the board
/Level Shifter 1/SIGNAL_HV: Q1.3 (D), R2.2; also elsewhere on the board
/PROTO_SIG_HV: Q3.3 (D), R8.2; also elsewhere on the board
/PROTO_SIG_LV: Q3.2 (S), R7.2; also elsewhere on the board
/SA: Q1.2 (S), R1.2; also elsewhere on the board

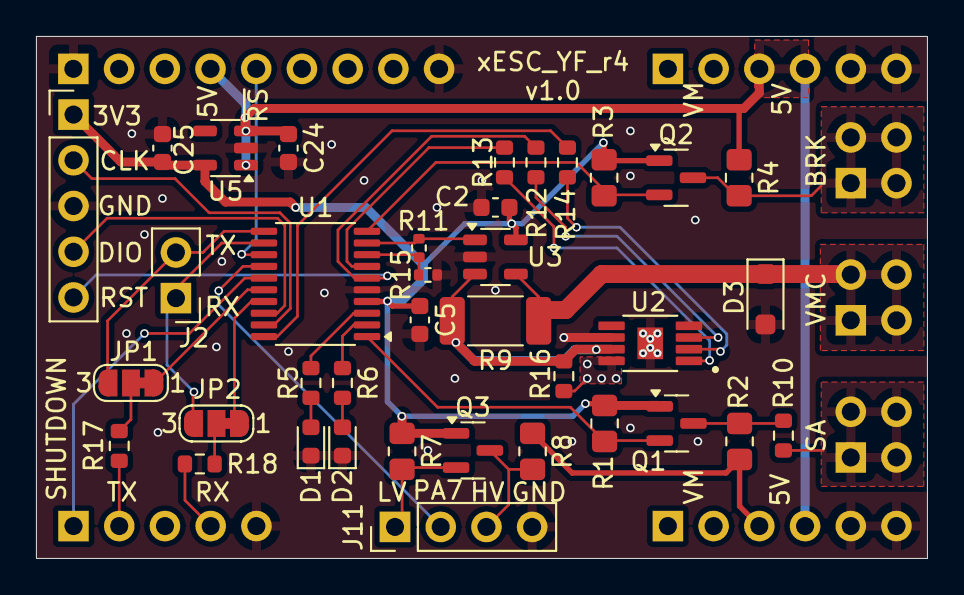
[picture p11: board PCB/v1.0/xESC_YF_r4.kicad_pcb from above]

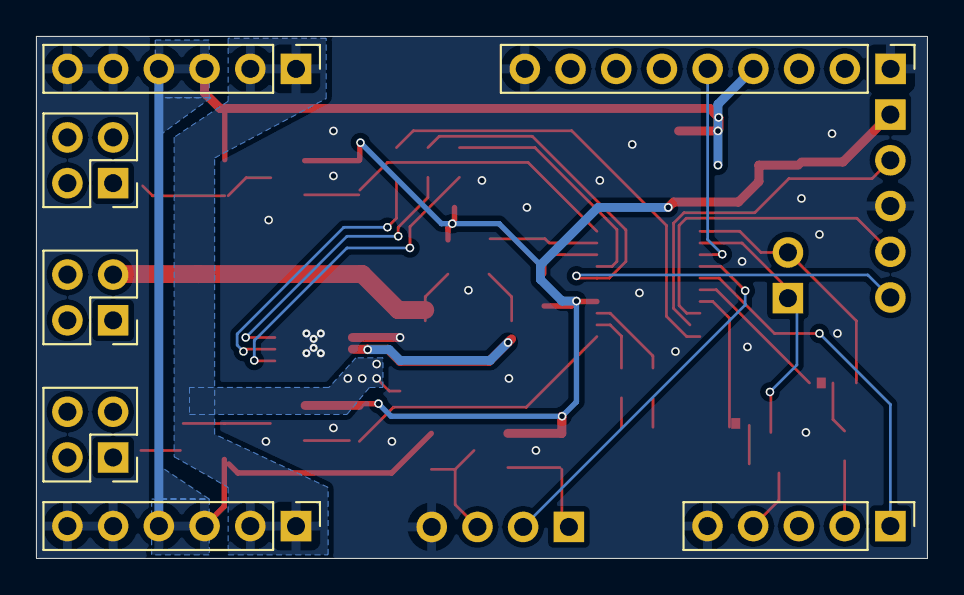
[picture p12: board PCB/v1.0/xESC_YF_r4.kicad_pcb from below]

Board: 2 copper layers, 49.5 x 29.0 mm, 44 parts (7 on the bottom side), 38 nets.

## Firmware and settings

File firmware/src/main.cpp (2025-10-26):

// Created by Apehaenger on 2024-06-14.
// Refactored by Jörg Ebeling on 2025-10-18.
//
// This file is part of the openmower project.
//
// This work is licensed under a Creative Commons
// Attribution-NonCommercial-ShareAlike 4.0 International License.
//
// Feel free to use the design in your private/educational projects, but don't
// try to sell the design or products based on it without getting my consent
// first.
//
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
#include <modm/platform.hpp>
#include <numeric>

#include "AdcSampler.hpp"
#include "board.hpp"
#include "config.h"
#include "debug.h"
#include "disable_nrst.hpp"
#include "hardware/hw_version.hpp"
#include "host_comm.hpp"
#include "led_controller.hpp"
#include "motor_control.hpp"
#include "xesc_yfr4_datatypes.h"

using namespace Board;
using namespace std::chrono_literals;

#define MILLIS modm::Clock::now().time_since_epoch().count()

// Global state.
bool wrong_hw = false;  // True if FW doesn't match detected HW

// LED GPIO objects.
ModmGpio<LedGreen> led_green_gpio;
ModmGpio<LedRed_v1> led_red_v1_gpio;
ModmGpio<LedRed_v2> led_red_v2_gpio;

// LED Controllers.
LedController status_led(&led_green_gpio);
#ifdef HW_V1
LedController error_led(&led_red_v1_gpio);
#else
LedController error_led(&led_red_v2_gpio);
#endif

// Status and settings packets.
XescYFR4StatusPacket status = {};

/**
 * @brief Update fault detection and LED indicators.
 */
void UpdateFaults() {
  static uint32_t last_fault_millis = 0;
  uint32_t faults = 0;
  bool is_shutdown = host::Shutdown::read();
  const auto& settings = host_comm::GetSettings();
  float cs_current = AdcSampler::getValue(AdcSampler::Sensors::CurrentSense);
  static uint8_t overcurrent_limit_count = 0;

  // FAULT_WRONG_HW_VERSION - Check if wrong hardware version firmware is running
  if (wrong_hw) {
    faults |= FAULT_WRONG_HW_VERSION;
  }

  // FAULT_UNINITIALIZED
  if (!host_comm::AreSettingsValid()) {
    faults |= FAULT_UNINITIALIZED;
  }

  // FAULT_WATCHDOG
  if (host_comm::HasWatchdogTimedOut()) {
    faults |= FAULT_WATCHDOG;
  }

  // FAULT_OVERTEMP_PCB
  if (AdcSampler::getValue(AdcSampler::Sensors::Temp) > (std::min(HW_LIMIT_PCB_TEMP, settings.max_pcb_temp))) {
    faults |= FAULT_OVERTEMP_PCB;
  }

#ifdef HW_V1
  // HW_V1: TPS1H200A via /FAULT pin
  if (!vm_switch::Fault::read()) {
    if (vm_switch::In::isSet()) {  // VM-Switch is "on"
      if (cs_current < 0.001f) {
        faults |= FAULT_OPEN_LOAD;
      } else {
        // Disabled because not clear how to detect
        // faults |= FAULT_OVERTEMP_PCB;
      }
    } else if (!is_shutdown) {
      faults |= FAULT_OPEN_LOAD;
    }
  }
#else
  // HW_V2: TPS1H100B fault detection via CS pin voltage
  // The TPS1H100B signals faults on the CS pin that we're already reading via ADC
  // According to datasheet:
  // - Normal operation: V_CS in linear region (0-4V), proportional to current
  // - Fault conditions: V_CS pulled to V_CS,h (typically ~5V, above ADC range)
  //   * Short to GND / Current limit
  //   * Thermal shutdown / Thermal swing
  // - Open load (ON-state): V_CS ≈ 0 (very low current)

  // Check for V_CS,h condition (fault signaling)
  // V_CS,h is typically 5V, but our ADC reads max 3.3V (VDDA)
  // If CS voltage is at or near VDDA, the actual voltage is likely higher (V_CS,h)
  static const float ICS_H_THRESHOLD = Board::adc::CalculateCurrent(3.2f);  // 97% of typical 3.3V VDDA

  if (vm_switch::In::isSet() && !is_shutdown) {
    // Motor should be running - check for faults
    if (cs_current >= ICS_H_THRESHOLD) {
      // V_CS,h detected - could be:
      // - Short to GND / Current limit
      // - Thermal shutdown
      // - Thermal swing
      // The TPS1H100B auto-recovers when fault clears
      faults |= FAULT_OVERCURRENT;  // Use existing fault code for now
    } else {
      // Only trigger open load if very low current happens a definable amount of times
      if (cs_current < 0.002f) {
        faults |= FAULT_OPEN_LOAD;
      }
    }
  } else if (!vm_switch::In::isSet() && !is_shutdown) {
    // Motor off - check for open load in off-state
    // In off-state with open load: CS pin pulled to V_CS,h
    if (cs_current >= ICS_H_THRESHOLD) {
      faults |= FAULT_OPEN_LOAD;
    }
  }
#endif

  // Handle FAULT_OVERCURRENT only if VMC is enabled and FAULT_OPEN_LOAD not already happen
  const float overcurrent_limit = std::min(HW_LIMIT_CURRENT, settings.motor_current_limit);
  if (vm_switch::In::isSet() && !(faults & FAULT_OPEN_LOAD) && cs_current > overcurrent_limit) {
    if (overcurrent_limit_count++ >= 10) {  // Require 10 consecutive overcurrent readings (200ms at 20ms status update)
      faults |= FAULT_OVERCURRENT;
    }
  } else {
    overcurrent_limit_count = 0;
  }

  // Enable/disable VMC based on faults, shutdown state or safely stopped motor
  // Do this after open-load or over-current evaluation, to give adc a chance to read the new values
  if (!(faults & FAULT_OPEN_LOAD) && !host::Shutdown::read()) {
    vm_switch::In::set();
    Timer1::enableInterrupt(motor::SACaptureInterrupt);
  } else if (motor_control::hasMotorSafelyStopped()) {
    Timer1::disableInterrupt(motor::SACaptureInterrupt);
    vm_switch::In::reset();
  }

  // Update LED indicators and status.fault_code
  if (faults) {
    status.fault_code = faults;
    last_fault_millis = MILLIS;

    // Update LED indicators based on fault priority.
    if (faults & FAULT_UNINITIALIZED) {
      status_led.Blink();  // 1Hz blink
    } else {
      status_led.Off();
    }

    if (faults & FAULT_WRONG_HW_VERSION) {
      error_led.On();
    } else if (faults & FAULT_OPEN_LOAD) {
      error_led.Blink(125U, 125U, 0);  // Quick blink (4Hz)
    } else if (faults & (FAULT_OVERTEMP_PCB | FAULT_OVERCURRENT)) {
      error_led.Blink(250U, 250U, 0);  // Fast blink (2Hz)
    } else if (faults & FAULT_WATCHDOG) {
      error_led.Blink(0, false);  // 1Hz blink
    }
  } else {
    // No faults - update status LED.
    if (is_shutdown) {
      status_led.Blink(
          {.on_time_ms = 100U, .off_time_ms = 1800U, .blink_cycle_limit = 1, .complete = true});  // Short pulse
    } else {
      status_led.On();
    }

    // Reset fault indication if cleared.
    if (status.fault_code != 0) {
      // Reset faults only if MIN_FAULT_TIME_MILLIS passed, or if it was a dedicated watchdog fault
      if (MILLIS - last_fault_millis > MIN_FAULT_TIME_MILLIS || status.fault_code == FAULT_WATCHDOG) {
        error_led.Off();
        status.fault_code = 0;
      }
    }
  }
}

/**
 * @brief Update status and handle faults - called every STATUS_CYCLE.
 */
void UpdateStatus() {
  static bool first_update = true;

  // Update fault detection and LED status.
  UpdateFaults();

  // Update motor state based on setpoint, faults and last tacho (20ms ago)
  motor_control::UpdateMotorState((status.fault_code != 0), host::Shutdown::read(), status.tacho);

  // Update status packet
  status.seq++;
  status.duty_cycle = motor_control::GetDuty();
  status.tacho = motor_control::GetSaTacho();
  status.tacho_absolute = motor_control::GetSaTacho();
  status.rpm = motor_control::GetRpm();
  status.temperature_pcb = AdcSampler::getValue(AdcSampler::Sensors::Temp);
  status.current_input = AdcSampler::getValue(AdcSampler::Sensors::CurrentSense);

#if (defined PROTO_DEBUG_COMMS || defined PROTO_DEBUG_MOTOR || defined PROTO_DEBUG_ADC)
  MODM_LOG_INFO << "TX status.fault_code=0x" << modm::hex << status.fault_code << modm::ascii;
#ifdef PROTO_DEBUG_MOTOR
  MODM_LOG_INFO << ", tacho=" << status.tacho << ", ticks=" << motor_control::GetSaTicks() << ", rpm=" << status.rpm;
#endif
#ifdef PROTO_DEBUG_ADC
  MODM_LOG_DEBUG << " Dirty=" << AdcSampler::getCacheDirty()
                 << " VRef=" << AdcSampler::getValue(AdcSampler::Sensors::VRef) << "V"
                 << " Temp=" << status.temperature_pcb << " CurrentSense=" << status.current_input << "A";
#endif
  MODM_LOG_INFO << modm::endl << modm::flush;
#endif

  // Disable ADC free running mode and manually start conversion to get fresh data for next status update
  if (first_update) {
    AdcSampler::switchToSingleShot();
    first_update = false;
  }
  // Before sending the status, trigger a new conversion for next cycle
  AdcSampler::triggerConversion();

  // Send status packet
  host_comm::SendMessage(&status, sizeof(status));
}

/**
 *
 * @brief Status Timer ISR - called every STATUS_CYCLE ms.
 */
MODM_ISR(TIM14) {
  Timer14::acknowledgeInterruptFlags(Timer14::InterruptFlag::Update);
  UpdateStatus();
}

int main() {
  // Initialize common hardware.
  Board::initialize();

#ifdef PROTO_DEBUG
  // Print hardware version info.
  MODM_LOG_INFO << "xESC_YF_rev4 - ";
  hardware::printVersionInfo(modm::log::info);
  MODM_LOG_INFO << modm::endl;
#endif

  // Check for hardware mismatch and initialize cross-version LEDs if needed.
  // SAFETY: We only initialize the GPIO for the OTHER hardware version
  // to avoid touching unknown GPIOs that might control motors or dangerous
  // hardware!
  if (!hardware::checkFlashMatchesBinary()) {
    wrong_hw = true;
#ifdef HW_V1
    // V1 binary on V2 hardware -> Initialize V2 LED GPIO.
    led_red_v2_gpio.SetOutput(Gpio::OutputType::PushPull);
    error_led.SetGpio(&led_red_v2_gpio);
#ifdef PROTO_DEBUG
    MODM_LOG_ERROR << "CRITICAL: V1 firmware on V2 hardware detected!" << modm::endl;
#endif
#else
    // V2 binary on V1 hardware -> Initialize V1 LED GPIO.
    led_red_v1_gpio.SetOutput(Gpio::OutputType::PushPull);
    error_led.SetGpio(&led_red_v1_gpio);
#ifdef PROTO_DEBUG
    MODM_LOG_ERROR << "CRITICAL: V2 firmware on V1 hardware detected!" << modm::endl;
#endif
#endif
  } else {
#ifdef HW_V1
    led_red_v1_gpio.SetOutput(Gpio::OutputType::PushPull);
#else
    led_red_v2_gpio.SetOutput(Gpio::OutputType::PushPull);
#endif
  }
  led_green_gpio.SetOutput(Gpio::OutputType::PushPull);

  // Hardware-specific initialization.
  if (!wrong_hw) {
    vm_switch::In::setOutput(Gpio::OutputType::PushPull);
    vm_switch::In::reset();  // VM-Switch, VMC = off
    vm_switch::DiagEnable::setOutput(Gpio::OutputType::PushPull);
    vm_switch::DiagEnable::reset();  // VM-Switch diagnostics disable because
                                     // Fault input get shared with NRST!!

    motor::SA::setInput(Gpio::InputType::Floating);  // Motor SA (Hall)
    motor::Brk::setOutput(Gpio::OutputType::PushPull);
    motor::Brk::reset();  // Motor BRK
    motor::RS::setOutput(Gpio::OutputType::PushPull);
    motor::RS::set();  // Motor !RS (Rapid/Rotor Start)

#ifdef HW_V1
    disable_nrst();                                       // Check NRST pin. Will flash if wrong and reset.
    vm_switch::DiagEnable::set();                         // V1 - safe only after disable_nrst()
    vm_switch::Fault::setInput(Gpio::InputType::PullUp);  // VM-Switch !FAULT signal (LowActive). Take
                                                          // attention to FAULT doesn't get triggered
                                                          // before NRST check
#else                                                     // HW_V2
    vm_switch::DiagEnable::set();  // V2+ - always safe to enable diagnostics
#endif
  }

  // Initialize subsystems
  AdcSampler::init();
  motor_control::Init();
  host_comm::Init();

  // Prepare status message.
  status.message_type = XESCYFR4_MSG_TYPE_STATUS;
  status.fw_version_major = 0;
  status.fw_version_minor = 3;
  status.direction = 0;  // Motor has only one direction

  // Status Timer.
  Timer14::enable();
  Timer14::setMode(Timer14::Mode::UpCounter);
  Timer14::setPeriod<Board::SystemClock>(STATUS_CYCLE);
  Timer14::enableInterrupt(Timer14::Interrupt::Update);
  Timer14::enableInterruptVector(true, 26);
  Timer14::applyAndReset();
  Timer14::start();

  // Boot-up success indication (3 quick blinks).
  status_led.QuickBlink(3, true);
  if (wrong_hw) {
    error_led.On();
  } else {
    error_led.QuickBlink(3, true);
  }

  // Main loop.
  while (true) {
    host_comm::ProcessUartData();
    status_led.Update();
    error_led.Update();
  }
}

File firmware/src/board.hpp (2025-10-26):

// Created by Apehaenger on 2024-06-14.
//
// This file is part of the openmower project.
//
// This work is licensed under a Creative Commons Attribution-NonCommercial-ShareAlike 4.0 International License.
//
// Feel free to use the design in your private/educational projects, but don't try to sell the design or products based
// on it without getting my consent first.
//
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

#ifndef MODM_XESCYFR4_BOARD_HPP
#define MODM_XESCYFR4_BOARD_HPP

#include <modm/platform.hpp>

#include "config.h"

#ifdef PROTO_DEBUG
#include <modm/debug/logger.hpp>
#endif

using namespace modm::platform;

namespace Board {
/// @ingroup modm_board_xescyfr4
/// @{
using namespace modm::literals;

struct SystemClock {
  static constexpr uint32_t Frequency = Rcc::HsiFrequency;  // 48MHz generated from internal RC
  static constexpr uint32_t Ahb = Frequency;
  static constexpr uint32_t Apb = 24_MHz;

  static constexpr uint32_t Adc1 = Apb;

  static constexpr uint32_t Spi1 = Apb;

  static constexpr uint32_t Usart1 = Apb;
  static constexpr uint32_t Usart2 = Apb;

  static constexpr uint32_t I2c1 = Apb;

  static constexpr uint32_t Timer1 = Apb;
  static constexpr uint32_t Timer2 = Apb;
  static constexpr uint32_t Timer3 = Apb;
  static constexpr uint32_t Timer14 = Apb;
  static constexpr uint32_t Timer16 = Apb;
  static constexpr uint32_t Timer17 = Apb;
  static constexpr uint32_t Iwdg = Rcc::LsiFrequency;
  static constexpr uint32_t Rtc = Rcc::LsiFrequency;

  static bool inline enable() {
    Rcc::enableLowSpeedInternalClock();
    Rcc::enableRealTimeClock(Rcc::RealTimeClockSource::Lsi);

    // 48MHz generated from internal RC
    Rcc::enableInternalClock();
    Rcc::setHsiSysDivider(Rcc::HsiSysDivider::Div1);
    // set flash latency for 48MHz
    Rcc::setFlashLatency<Frequency>();
    // switch system clock to PLL output
    Rcc::setAhbPrescaler(Rcc::AhbPrescaler::Div1);
    Rcc::setApbPrescaler(Rcc::ApbPrescaler::Div2);  // 24 MHz for APB
    // update frequencies for busy-wait delay functions
    Rcc::updateCoreFrequency<Frequency>();

    return true;
  }
};

using LedGreen = GpioC15;

// Hardware version specific LEDs (always define both for cross-version error indication)
using LedRed_v1 = GpioC14;
using LedRed_v2 = GpioB6;

// Alias for the correct red LED based on compiled hardware version
#ifdef HW_V1
using LedRed = LedRed_v1;
#else
using LedRed = LedRed_v2;
#endif
/// @}

namespace host {
/// @ingroup modm_board_xescyfr4
/// @{
using Tx = GpioOutputA9;
using Rx = GpioInputA10;
using Uart = BufferedUart<UsartHal1, UartTxBuffer<32>, UartRxBuffer<32>>;
#ifdef HW_V1
using Shutdown = GpioInputA8;
#else
using Shutdown = GpioInputC14;
#endif
/// @}
}  // namespace host

namespace proto_uart {
/// @ingroup modm_board_xescyfr4
/// @{
using Tx = GpioOutputA4;
using Rx = GpioInputA5;
using Uart = BufferedUart<UsartHal2, UartTxBuffer<32>>;
/// @}
}  // namespace proto_uart

// VM-Switch
namespace vm_switch {
/// @ingroup modm_board_xescyfr4
/// @{
#ifdef HW_V1
using In = GpioOutputA0;          // IN (High = VMC-on)
using DiagEnable = GpioOutputB6;  // DIAG_EN (High = Diagnostics on)
using Fault = GpioInputF2;        // !FAULT (Low = Fault detected)
#else
using In = GpioOutputA1;          // IN (High = VMC-on)
using DiagEnable = GpioOutputA2;  // DIAG_EN (High = Diagnostics on)
#endif
/// @}
}  // namespace vm_switch

// Motor
namespace motor {
/// @ingroup modm_board_xescyfr4
/// @{
#ifdef HW_V1
using SA = GpioInputB7;                                                         // Motor SA (Hall)
using SATimChan = SA::Ch4;                                                      // SA timer channel
static constexpr auto SACaptureInterrupt = Timer1::Interrupt::CaptureCompare4;  // SA timer capture/compare interrupt
static constexpr auto SACaptureFlag = Timer1::InterruptFlag::CaptureCompare4;   // SA timer capture/compare flag
using Brk = GpioOutputA3;                                                       // Motor BRK
using RS = GpioOutputA6;  // Motor !RS (Rapid/Rotor Start) (LowActive)
#else
using SA = GpioInputA0;                                                         // Motor SA (Hall)
using SATimChan = SA::Ch1;                                                      // SA timer channel
static constexpr auto SACaptureInterrupt = Timer1::Interrupt::CaptureCompare1;  // SA timer capture/compare interrupt
static constexpr auto SACaptureFlag = Timer1::InterruptFlag::CaptureCompare1;   // SA timer capture/compare flag
using Brk = GpioOutputA6;                                                       // Motor BRK
using RS = GpioOutputA8;  // Motor !RS (Rapid/Rotor Start) (LowActive)
#endif
/// @}
}  // namespace motor

namespace adc {
/// @ingroup modm_board_xescyfr4
/// @{
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

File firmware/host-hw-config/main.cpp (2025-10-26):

// Hardware config generator - generates minimal flash config binaries

#include <iostream>
#include <fstream>
#include <cstdint>
#include <string>
#include <sys/stat.h>
#include <sys/types.h>
#include <cstring>

// Include the flash config
#include "../include/hardware/hw_version.hpp"

// Hardware version configurations
struct HardwareVersionConfig {
    uint8_t major;
    uint8_t minor;
    const char* name;
};

// Available hardware versions
const HardwareVersionConfig hw_configs[] = {
    {1, 0, "v1.0"},
    {2, 0, "v2.0"}
};

bool GenerateConfigBinary(const HardwareVersionConfig& hw_config, const std::string& output_file) {
    // Create the flash config structure
    hardware::FlashHardwareConfig flash_config;

    // Set magic string using the shared constant
    strcpy(flash_config.magic, hardware::HARDWARE_CONFIG_MAGIC);

    // Set version
    flash_config.version.major = hw_config.major;
    flash_config.version.minor = hw_config.minor;

    // Calculate CRC over everything except the CRC field itself
    uint16_t crc = hardware::calculateCrc16CcittFalse(
        reinterpret_cast<const uint8_t*>(&flash_config),
        sizeof(hardware::FlashHardwareConfig) - sizeof(flash_config.crc16)
    );
    flash_config.crc16 = crc;

    // Write binary file
    std::ofstream file(output_file, std::ios::binary);
    if (!file) {
        std::cerr << "Error: Cannot create " << output_file << std::endl;
        return false;
    }

    file.write(reinterpret_cast<const char*>(&flash_config), sizeof(flash_config));
    file.close();

    std::cout << "Generated " << output_file << ": " << hw_config.name
        << " (v" << static_cast<int>(hw_config.major) << "." << static_cast<int>(hw_config.minor) << ")"
        << ", Size=" << sizeof(flash_config) << " bytes"
        << ", CRC=0x" << std::hex << crc << std::dec << std::endl;

    return true;
}

int main(int argc, char* argv[]) {
    std::cout << "=== Hardware Config Generator ===" << std::endl;
    std::cout << "Generating hardware config binaries..." << std::endl;

    // Use output directory from command line argument if provided
    std::string output_dir = ".";
    if (argc > 1) {
        output_dir = argv[1];
        // Create output directory if it doesn't exist
        mkdir(output_dir.c_str(), 0755);
    }

    bool success = true;

    // Generate all available hardware configurations
    for (const auto& hw_config : hw_configs) {
        std::string filename = output_dir + "/hw_config_v" +
            std::to_string(hw_config.major) + "." +
            std::to_string(hw_config.minor) + ".bin";
        success &= GenerateConfigBinary(hw_config, filename);
    }

    if (success) {
        std::cout << "All hardware config binaries generated successfully." << std::endl;
        std::cout << "These can now be flashed to OTP flash address 0x1FFF7000." << std::endl;
        return 0;
    } else {
        std::cerr << "Failed to generate some hardware config binaries!" << std::endl;
        return 1;
    }
}

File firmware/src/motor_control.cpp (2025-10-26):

// Created by Jörg Ebeling on 2025-10-18.
// Copyright (c) 2025 Jörg Ebeling for OpenMower/Clemens Elflein. All rights reserved.
//
// This work is licensed under a Creative Commons
// Attribution-NonCommercial-ShareAlike 4.0 International License.
//
// Feel free to use the design in your private/educational projects, but don't
// try to sell the design or products based on it without getting my consent
// first.
//
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
#include "motor_control.hpp"

#include <modm/architecture.hpp>
#include <modm/platform.hpp>

#include "board.hpp"
#include "config.h"

using namespace Board;

namespace motor_control {

// Internal state.
namespace {
volatile float duty_ = 0.0f;
float duty_setpoint_ = 0.0f;
volatile uint32_t sa_ticks_ = 0;
volatile uint32_t sa_tacho_ = 0;
volatile uint16_t rpm_ = 0;
uint8_t motor_stopped_cycles_ = 0;
}  // namespace

/**
 * @brief SA (Hall sensor) Capture/Compare ISR.
 *
 * Timer configuration:
 * - 16-bit up-counter (0xFFFF max)
 *
 * Overflow handling: When timer overflows between captures, the difference
 * calculation automatically handles it via 32-bit arithmetic.
 */
MODM_ISR(TIM1_CC) {
  static uint8_t skip_initial = 10;
  static uint16_t last_cc_value = 0;
  uint16_t current_cc_value = Timer1::getCompareValue<motor::SATimChan>();

  // Didn't got rid of initial spurious interrupts yet?
  if (skip_initial > 0) {
    skip_initial--;
    last_cc_value = current_cc_value;
    return;
  }

  Timer1::acknowledgeInterruptFlags(motor::SACaptureFlag);
  sa_tacho_++;

  if (Timer1::getInterruptFlags() & Timer1::InterruptFlag::Update) {
    Timer1::acknowledgeInterruptFlags(Timer1::InterruptFlag::Update);
    // Timer overflow occurred between captures
    sa_ticks_ = current_cc_value + (0xffff - last_cc_value);
  } else {
    // Normal case: no overflow
    sa_ticks_ = current_cc_value - last_cc_value;
  }
  last_cc_value = current_cc_value;

  // RPM calculation with new timer configuration:
  // Timer frequency = 24MHz / 220 = 109'090 Hz = 9.1667 μs per tick
  // Hall sensors: 4 poles * 2 edges per pole = 8 edges per revolution
  //
  // Time per revolution = sa_ticks_ * 9.1667 μs * 8 edges = sa_ticks_ × 73.333 μs
  // RPM = 60 / (time per revolution in minutes) = 60 / (sa_ticks_ / 109'090 / 60)
  // Simplified: RPM = (109'090 × 60) / (sa_ticks_ × 8)

  // Break down calculation for clarity:
  // timer_frequency = Board::SystemClock::Timer1 / (SA_TIMER_PRESCALER + 1);
  // seconds_per_minute = 60;
  // edges_per_revolution = 8;
  // schwund = 2;
  // rpm_divisor = (timer_frequency * seconds_per_minute) / edges_per_revolution;
  constexpr uint32_t rpm_divisor = ((Board::SystemClock::Timer1 / (SA_TIMER_PRESCALER + 0)) * 60) / 8 * 2;

  if (sa_ticks_ > 0) {
    rpm_ = rpm_divisor / sa_ticks_;
  } else {
    rpm_ = 0;
  }
}

void Init() {
  // SA (Hall) input - Capture/Compare timer.
  Timer1::connect<motor::SATimChan>();
  Timer1::enable();
  Timer1::setMode(Timer1::Mode::UpCounter);
  Timer1::setPrescaler(SA_TIMER_PRESCALER);
  Timer1::setOverflow(0xFFFF);
  Timer1::configureInputChannel<motor::SATimChan>(Timer1::InputCaptureMapping::InputOwn,
                                                  Timer1::InputCapturePrescaler::Div1,
                                                  Timer1::InputCapturePolarity::Both, SA_TIMER_INPUT_FILTER);
  Timer1::enableInterrupt(motor::SACaptureInterrupt);
  Timer1::enableInterruptVector(motor::SACaptureInterrupt, true, 21);
  Timer1::applyAndReset();
  Timer1::start();
}

void SetDutySetpoint(float duty) {
  duty_setpoint_ = duty;
}

float GetDuty() {
  return duty_;
}

// Update motor state based on faults, shutdown signal and current tacho.
// Handles also BRK release once safely stopped.
void UpdateMotorState(bool has_faults, bool is_shutdown, uint32_t last_tacho) {
  float new_duty = (has_faults || is_shutdown) ? 0.0f : duty_setpoint_;

  // Handle safe stop and BRK release
  if (new_duty == 0.0f) {
    UpdateMotorStoppedState(last_tacho);
  }

  if (new_duty == duty_) return;

  if (new_duty == 0.0f) {
    // Stop motor.
    motor::RS::set();   // !RS off
    motor::Brk::set();  // Brake
  } else {
    // Start motor.
    motor::Brk::reset();  // Release brake
    motor::RS::reset();   // !RS on
  }
  duty_ = new_duty;
  motor_stopped_cycles_ = 0;
}

uint32_t GetSaTacho() {
  return sa_tacho_;
}

uint32_t GetSaTicks() {
  return sa_ticks_;
}

uint16_t GetRpm() {
  return rpm_;
}

bool hasMotorSafelyStopped() {
  return (motor_stopped_cycles_ > NUM_STATUS_CYCLES_MOTOR_STOPPED);
}

bool UpdateMotorStoppedState(uint32_t last_tacho) {
  if (sa_tacho_ == last_tacho) {
    // Motor appears stopped (same tacho value) but at very low RPM tacho might not change every cycle
    if (hasMotorSafelyStopped()) {
      sa_ticks_ = 0;
      rpm_ = 0;
      motor::Brk::reset();  // Release brake
      return true;
    } else {
      motor_stopped_cycles_++;
    }
  } else {
    motor_stopped_cycles_ = 0;
  }
  return false;
}

}  // namespace motor_control

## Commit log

2024-06-01 Initial concept
    [xESC2.kicad_pcb, xESC2.kicad_sch]
2024-06-01 added pinout
    [xESC2.kicad_sch]
2024-06-05 Schematics and PCB done
    [LEVEL_SHIFTER.kicad_sch, xESC2.kicad_pcb, xESC2.kicad_sch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]
2024-06-06 Change current sense parts and add SA protection
    [xESC_FY_r4.kicad_sch]
2024-06-10 Bootloader capable UART, high-side power switch, free-wheeling safety, current sense adjustment
    [xESC_FY_r4.kicad_pcb, xESC_FY_r4.kicad_sch]
2024-06-11 Fix fille names and VMC area
    [xESC_YF_r4.kicad_pcb, xESC_YF_r4.kicad_sch]
2024-06-11 2 stage current sense with 20/40 gain
    [LEVEL_SHIFTER.kicad_sch, xESC_YF_r4.kicad_pcb, xESC_YF_r4.kicad_sch]
2024-06-11 Open-load detection
    [xESC_YF_r4.kicad_pcb, xESC_YF_r4.kicad_sch]
2024-06-12 Fix DRC issues
    [xESC_YF_r4.kicad_pcb, xESC_YF_r4.kicad_sch]
2024-06-12 Remove bad/old symbol & footprint libs
    [xESC_YF_r4.kicad_pcb]
2024-06-12 UART protection
    [xESC_YF_r4.kicad_pcb, xESC_YF_r4.kicad_sch]
2024-06-20 Fix high impedance SA input and remove proto parts
    [LEVEL_SHIFTER.kicad_sch, xESC_YF_r4.kicad_pcb, xESC_YF_r4.kicad_sch]
2024-06-20 OpenOCD with STM32C0x support
    [100ask-openjtag.cfg, 8devices-lima.cfg, actux3.cfg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]
2024-06-20 Fix obsolete parts
    [xESC_YF_r4.kicad_pcb]
2024-06-23 Finish current state before refactor
2024-06-25 Applied xesc_ros::xesc_yfr4 driver
2024-07-08 Open VMC detection and own LED lib to save 2.6k flash
2024-07-09 Fix LED class so that comms-error-Flash can't look like LED on
    [main.cpp]
2024-07-10 Add FAILURE detection and Disable-NRST pin
    [main.cpp]
2024-07-11 Tried ADC but no space left for debugging
2024-07-15 Add board and adapted a couple of project settings
2024-07-15 Switch to CMake
2024-07-19 Migrate previous LED class as LedSeq class template
2024-08-04 Finished VMC power, start, stop, break, tacho and rpm
2024-08-05 Automatic disable of NRST pin
2024-08-05 Add alternative SA parts
    [xESC_YF_r4.kicad_sch]
2024-08-08 Archive PCB v1.0 and start v2.0
    [LEVEL_SHIFTER.kicad_sch, bom_jlcpcb.xls, xESC_YF_r4.kicad_pcb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]
2024-08-16 Add ADC stuff (VRef, Current, PCB-Temp)
2024-08-16 Add measurements
    [xESC_YF_r4.kicad_sch]
2024-08-16 Change PCB folder structure
    [LEVEL_SHIFTER.kicad_sch, bom_jlcpcb.xls, xESC_YF_r4.kicad_pcb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]
2024-08-18 Add shutdown signal handling
    [xESC_YF_r4.kicad_sch]
2024-08-18 Fix SA-Timer NVIS priority and CaptureCompare filter
    [config.h, main.cpp]
2024-08-18 Add handlimng of temperature and current limits
2024-08-18 Add shutdown LED sequence
2024-08-20 Add STM32 bootloader support via trigger string
2024-10-03 Switch to mainline modm branch
2024-10-03 Squashed commit of the following: - Switch to mainline modm branch - Merge branch 'feature/RPM' into develop - Add RPM to status package
2025-08-21 Add HW v2.0
    [bom_jlcpcb.xls, xESC_YF_r4.kicad_sch, xESC_YF_r4_4Layer.kicad_pcb]
2025-08-21 Branch in HW v2.0
    [bom_jlcpcb.xls, xESC_YF_r4.kicad_pcb, xESC_YF_r4.kicad_sch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]
